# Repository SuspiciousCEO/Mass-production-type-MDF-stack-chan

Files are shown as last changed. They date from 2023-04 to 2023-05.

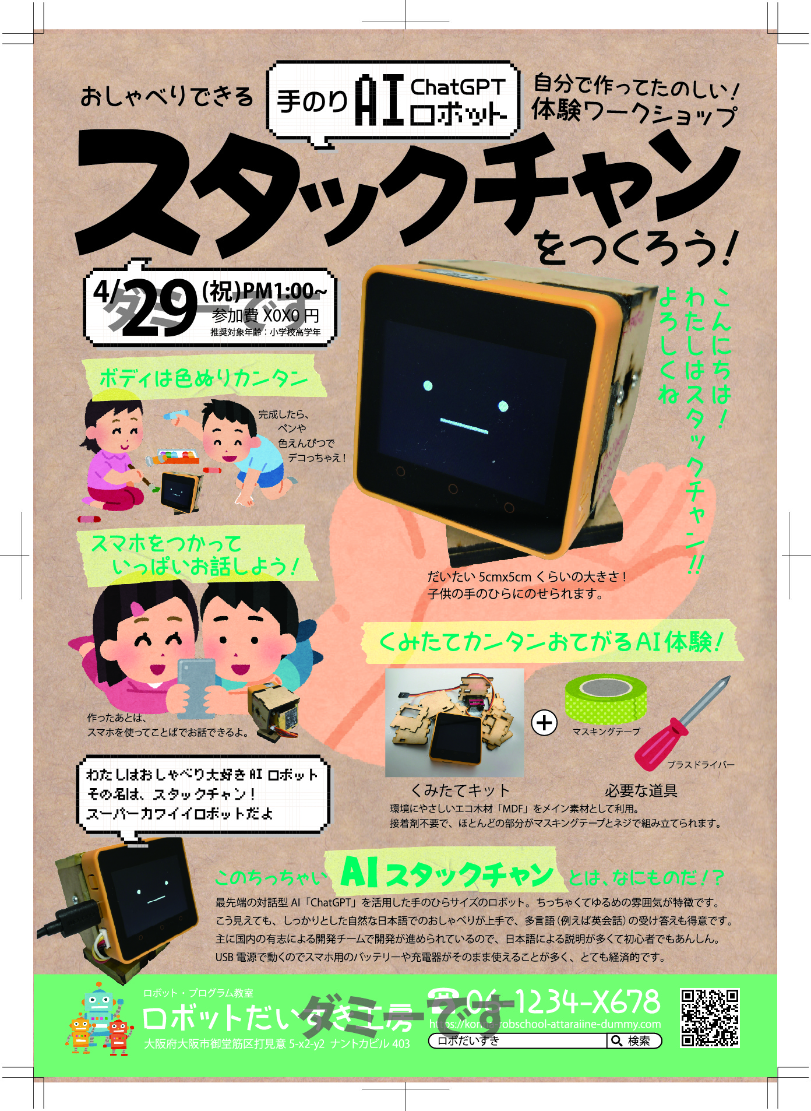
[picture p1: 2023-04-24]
FlyerDummy230327A.jpg

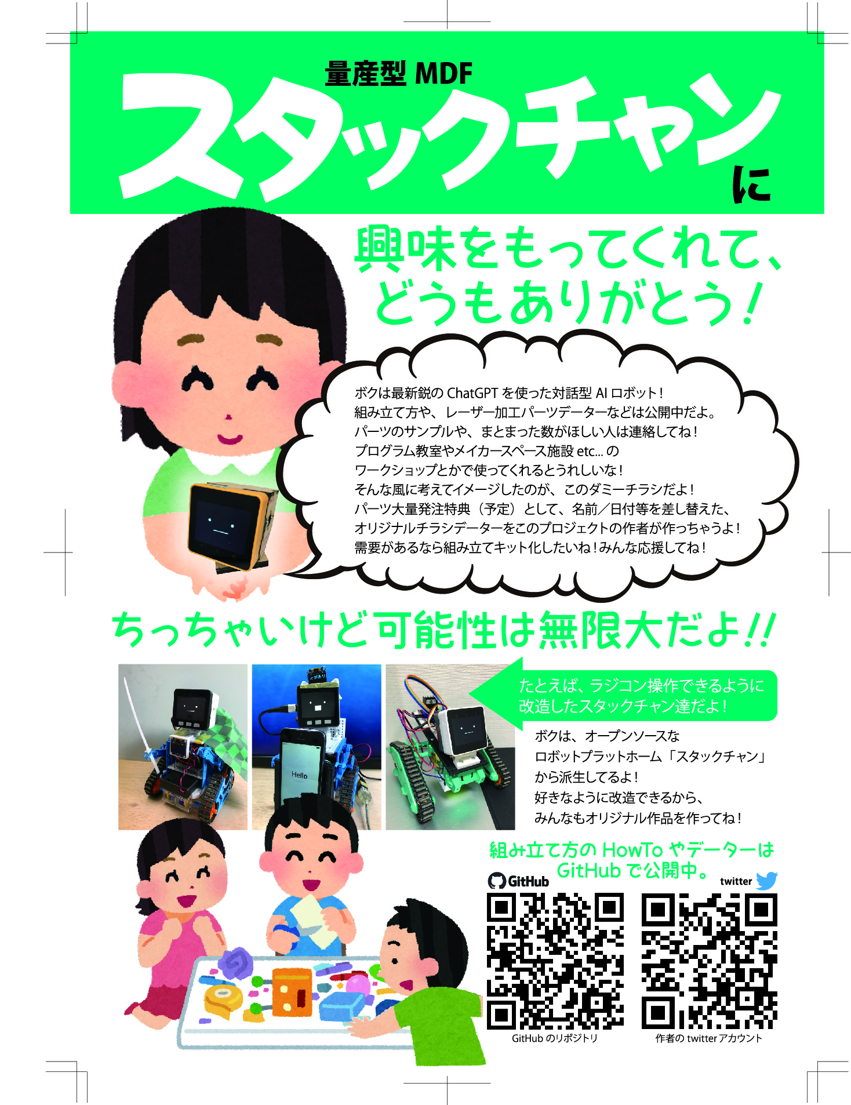
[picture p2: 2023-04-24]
FlyerDummy230327B.jpg

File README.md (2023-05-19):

# 量産型MDFｽﾀｯｸﾁｬﾝ



これはスーパーカワイイロボット [ｽﾀｯｸﾁｬﾝ(Stack-chan)](https://github.com/meganetaaan/stack-chan)
を量産しやすいように筐体ボディケースをMDF2.5mm厚用に設計したものです。
可能なかぎり、オリジナルのｽﾀｯｸﾁｬﾝSG90版筐体ボディとの動作の互換性を持たせています。
筐体ボディは共通部分が多いので、他の派生ｽﾀｯｸﾁｬﾝ（たとえば[AIｽﾀｯｸﾁｬﾝ](https://github.com/robo8080/M5Unified_StackChan_ChatGPT)
など）でもそのまま使うことが可能でしょう。

※写真は開発途中のものです。

## 特徴

オリジナルの[3Dプリンター版ｽﾀｯｸﾁｬﾝ](https://github.com/meganetaaan/stack-chan/tree/dev/v1.0/case)に比べ以下の点が優れています。





### 組み立てと分解が簡単
**小学生高学年でも作れそうなレベルを目指しました。**
たとえ破損したとしてもそのパーツの部分だけを追加で用意することで、全体のパーツを無駄にすることなく組み立てを再開することが可能です。
後述しますが、材料が安価なので失敗に対しての心構えが楽ですし、予備を多めに用意したとしても予算を圧迫しません。

### 適度な難易度とスピード感
材料が揃っていれば慣れてくると大人なら30分ぐらいで物理的な組み立て完了が可能。
失敗や手戻りがあったとしても、マスキングテープを剥がせばいいだけなので、特にパーツが痛むこともなく再開できます。
接着剤だと、固まり切ったらやり直しが難しいでしょうからこうはいきません。
あらかじめ時間枠が決まっている授業やワークショップなどでの活用に適しています。

### 圧倒的な生産性
レーザー加工機でパーツを切り出して用意するのに、一体につき10分もかかりません。(20Wくらいの出力ができる機種を想定)
3Dプリンター版を出力した場合、一体につき約半日〜1日の時間が必要となります。
また3Dプリンターによる造形物出力は、時には失敗することもあります。
期日までにまとまった数を用意することが必要な教育現場において、生徒全員に行き渡らせる必要がある教材を3Dプリンター出力に頼るのは不安が残りますが、
この量産型であればそういった懸念を払拭できます。

### 安い！コストパフォーマンス良好
筐体ボディ部分がMDF2.5mm厚板A5サイズで1枚に収まるので、極めて安価。
これ以外に組み立てで必要となる部品。すなわち頭脳部分になるマイコンM5Stackとサーボモーター類に予算を振り分けることが可能です。

### 安全性について
パーツさえそろっていれば、ボンドや接着剤類を使わなくても組み立てが可能。（もちろん使ってもOK）
組み立てに必要な道具はマスキングテープとプラスドライバー、あとお好みで結束バンドを。
刃物を使ったりしないのでケガをしにくいです。

### カスタマイズできる
子供達でも扱いが容易な3DCADソフトウェアのTinkercadで[プロジェクトデーター](https://www.tinkercad.com/things/7WoQx0e2Eym)を公開しているので、
その気になれば自由に再設計が可能です。

### 木のぬくもり感と後加工が容易
MDFは木材と紙の両方の雰囲気があるので、絵具などで色塗したり。ハサミなどであとからチョキチョキも可能。
キリやピンバイス（ハンドドリル）で穴あけも容易です。
紙を貼り合わせる場合でも水性のりでくっつくので接着剤を必要としません。
組み立て後も、カスタマイズの自由度が高いので自分ならではのオリジナル作品にすることができます。

### 持ち運びしやすい
組み立てやすくて、分解しやすいので、マスキングテープを剥がせば再び平面状にすることが可能。
よって普通郵便やメール便などで低コストに発送が可能です。
オリジナル版は約5cm立方サイズよりも小さくすることができないので、発送方法は少し考える必要があります。

## 欠点（ただし解決策や妥協点はあり）


### レーザー加工機が必要
あらかじめ、レーザー加工機でMDF板からパーツを切り出す必要があります。
（もちろんカッターナイフを使って手で切り出すことも可能かもしれませんがおすすめしません。）
レーザー加工機は個人宅で所有運用するには敷居が高いものですが、
教育機関やFab施設やホームセンターなどでも加工を請け負う場所が増えています。
それら加工業者などに依頼すれば比較的安価に切り出し加工が可能です。

### ススや焦げがある
レーザー加工機で焼き切っているので、どうしてもコゲとススはご愛嬌です。
気になるようでしたら、作業前に使い古しの歯ブラシでこすったり、ウェットティッシュで拭き取ってみてください。
ダイレクトに水洗いするとMDFは木と紙の間くらいの材質なので、ふやけてモロモロになってしましますので注意。

### 精度がすこしゆるい。
ハンドメイドなのでどうしても精度が甘くなりがちですが、ある程度ユルくても問題なく動くのであまり気にしなくてもいいです。

### 全てのサーボモーターに適合するかはやってみなければわからない
SG90というホビー向けサーボモーターは類似品が多く出回っており、入手性が良好な反面、おかげで動作やサイズに個体差やばらつきがあり、相性問題が発生します。必ずしも挙動やサイズ寸法がまったく同じというわけにはなっていません。

## 必要なもの


●本データーで切り出したMDF2.5mm厚パーツ一式、（2.5mm厚であればベニア等でも可）

●M5Stack CORE2（構成がほぼ同一のAWS版やおそらくBasicでも可）

●SG90系サーボモーター2個（サーボホーンやネジ類も付属してることが多いです。）

●[専用基板](https://github.com/akita11/Stack-chan_Takao_Base)

●Groveケーブル

●M3x6mmナベネジ1本

●M3x10mmナベネジ2本
※M3x10座金組込みねじ(セムスねじ)でもOK

●M3x18mmナベネジ4本
※Basicの場合、2本のみ、また18mmは長すぎるので付属スペーサーを追加するとよい

●M3ナット2個

●M3x6mmタップタイトねじPナベ4本

●SG90系サーボモーター2個

●マスキングテープ

●+ドライバー

●結束バンド （お好みで。）

●木工ボンド（マスキングテープの強度では不満がある場合はお好みで。）

## 組み立て方（マスキングテープ版）


### パーツAを2枚重ねて貼り合わせる


### パーツAを骨組みにして、パーツB・C・Dを組み合わせて貼る。これをヘルメット部分としておきます。



### 足部分を作る。パーツE・F・Eをはさんで貼る。



### パーツHに[専用基板](https://github.com/akita11/Stack-chan_Takao_Base)を取り付ける



輪っかの形をしているスペーサーを間にはさみながら、M3x10ネジとナットを使って締め付けます。

外側＞ [M3x6ネジ] | [パーツH] | [スペーサー] | [専用基板] | [ナット] ＜内側

### 胴体部分を作る。パーツG・H・I・J・Kを組み合わせて、箱状態にする。



### 足部分（パーツE・F・E）にサーボホーンをサーボモーターに付属のネジで固定。



サーボホーンの向きに注意。真ん中の形状をよく見て、細かいギザギザが中央部分にあるのがサーボモーター内側になります。
このとき使うサーボモーターに付属しているネジは、先が少し尖っているので注意。

### 胴体部分にサーボモーター2個を取り付ける。M3x6mmタップタイトねじPナベネジで固定。



先に下部の足用サーボモーターを取り付けてから、ヘルメット用のサーボモーターを取り付けます。
この時、ネジがすこし斜めになりやすいので、なるべく垂直にネジを締めましょう。

### ケーブルをまとめます。



ケーブル類が長くて邪魔なので、なるべく胴体内に束ねるように詰め込みます。
このとき、あとの作業がやりやすいように、胴体の穴からコネクター部分を外へくぐらせておきましょう。

### 結束バンドでケーブルを束ねてしばります。


結束バンドをしばって余った部分は、ニッパーなどで切りとりますが、切り口の先が尖らないように注意。

### ヘルメット部分にサーボホーンを取り付けます。



サーボホーンの片方が長くてジャマになるので、ニッパーなどですこし先の部分を切りとります。このとき使うサーボモーターに付属しているネジは、先が少し尖っているので注意。

### 胴体とヘルメット部分をつなげ合わせます。



サーボモーターの軸とサーボホーンの穴に合わせてはめ込みます。
ここはすこし難しいかもしれませんので、ヘルメット部分を手ですこし広げて強引に入れるか、一度ヘルメット部分のテープをはがして分解してからサーボホーンの穴に合わせてはめ込んだ後、再度ヘルメット部分を貼り合わせて元に戻すようにしてみるのも良いでしょう。

### サーボモーターとサーボホーンをねじ止めします。



先にM3x6mmタップタイトねじPナベをサーボに仮でネジ締めを通したほうがあとあとやりやすい。
足部分の裏側からサーボモーターをねじ止めします。同様にヘルメット部分のサーボモーターもねじ止めします。

### ヘルメット部分にM5Stack本体を裏側からネジ止めします。



M3x18mmナベねじを使って固定します。あまりキツくしめると、液晶画面を痛めるのでほどほどに。ネジ穴部分に指が届きにくいのですこしコツがいります。難しいようでしたら、一度ヘルメット部分のテープをはがして分解してからネジ止めして、再度ヘルメット部分を貼り合わせて元に戻すようにしてみるのも良いでしょう。

### 仕上げにGroveコネクタをM5Stack本体側面につなげて完成。



ヘルメット部分の残ったネジ穴にM3x6mmナベねじを少しゆるめに入れます。ネジは空回りするのですが、それが正解です。軸の固定は反対側のサーボホーンでしっかり強度があるのであまり気にしないで。最後にGroveコネクタをM5Stack本体側面につなげて完成です。

## その他



量産型ロボットの様式美として、稼働範囲の自由度を上げるために、動力線を一部筐体ボディ外部に露出させてあります。

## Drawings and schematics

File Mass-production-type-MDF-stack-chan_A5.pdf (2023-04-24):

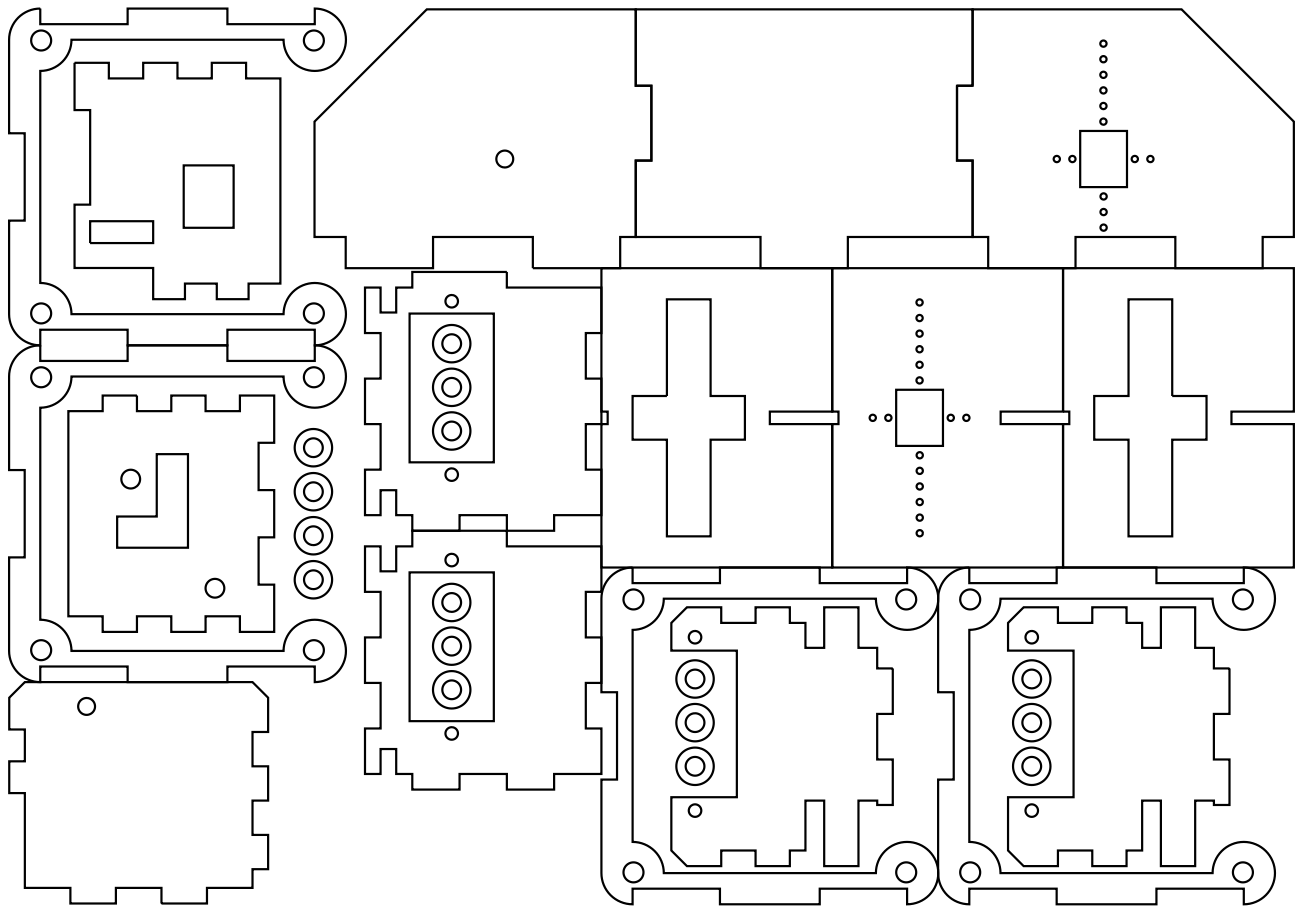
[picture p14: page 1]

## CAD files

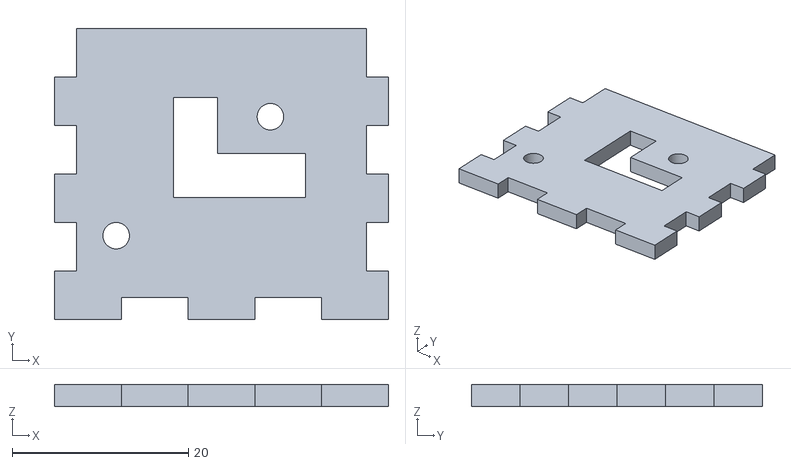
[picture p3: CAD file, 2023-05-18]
MDFstackchanH.stl
37.9 x 33.0 x 2.50

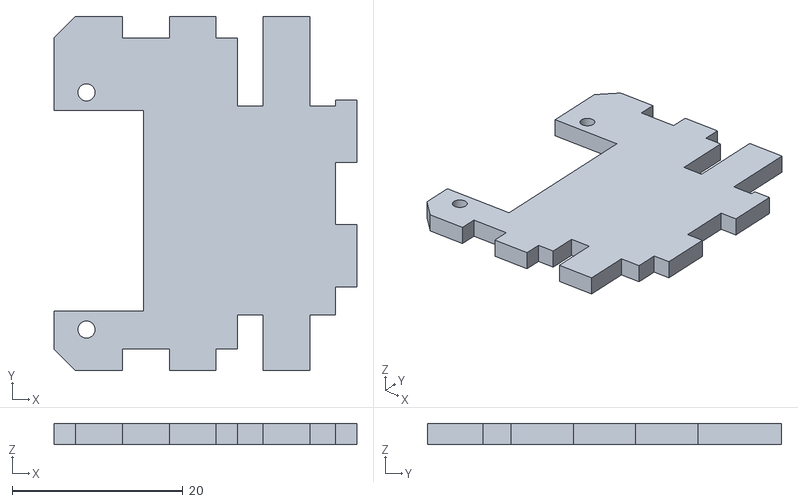
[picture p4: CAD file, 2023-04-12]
MDFstackchanJ.stl
35.5 x 41.5 x 2.50

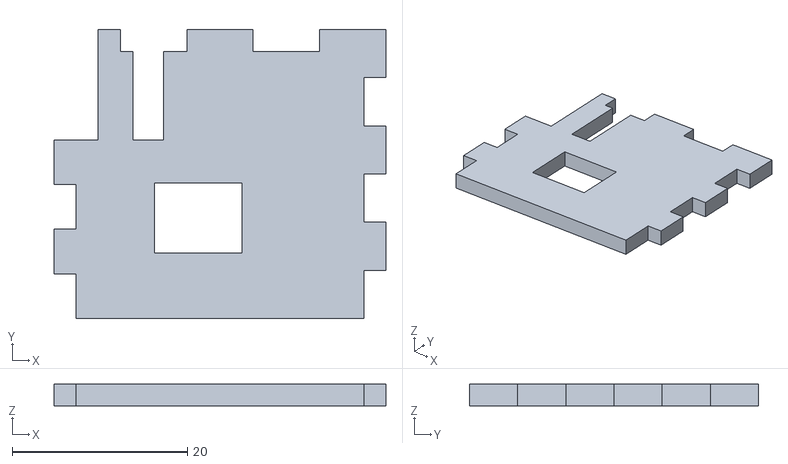
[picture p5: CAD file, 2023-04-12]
MDFstackchanG.stl
37.9 x 33.0 x 2.50

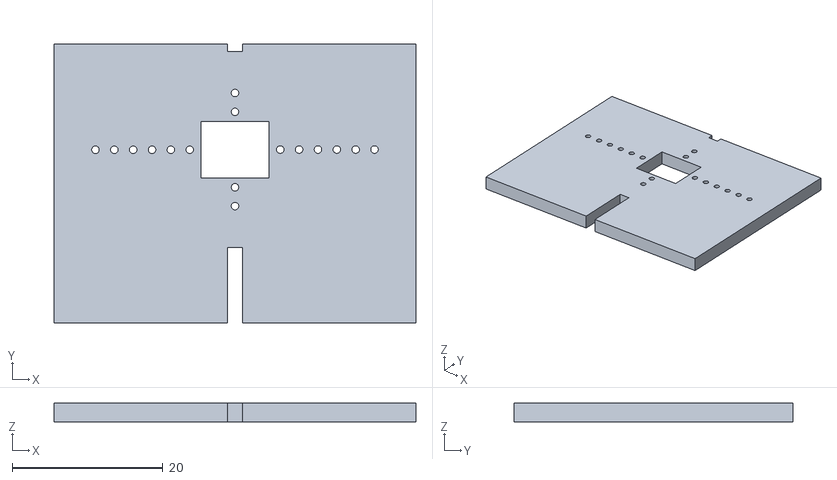
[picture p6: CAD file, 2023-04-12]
MDFstackchanF.stl
48.0 x 37.0 x 2.50

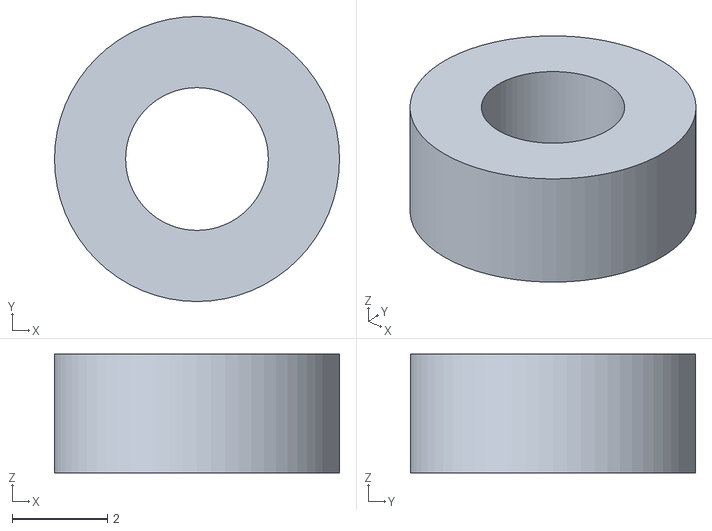
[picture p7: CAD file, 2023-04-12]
MDFstackchanL.stl
6.00 x 6.00 x 2.50

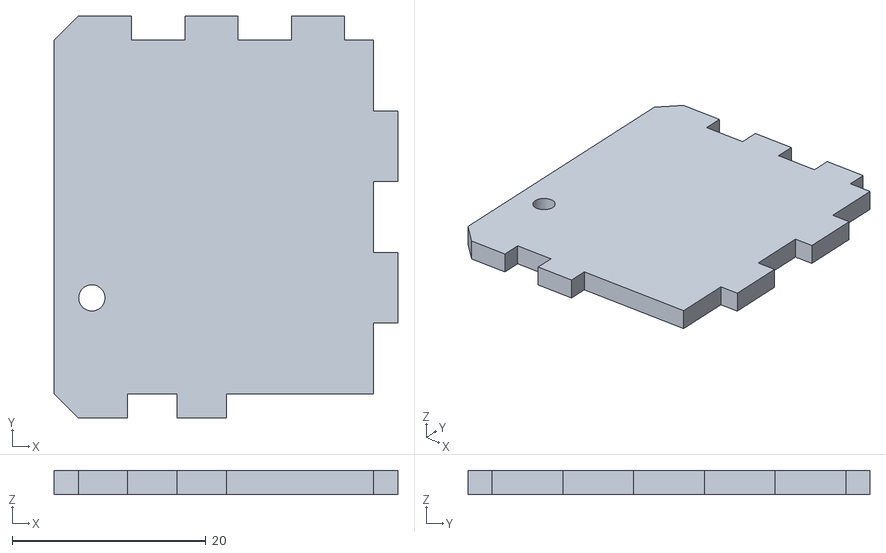
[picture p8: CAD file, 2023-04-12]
MDFstackchanI.stl
35.5 x 41.5 x 2.50

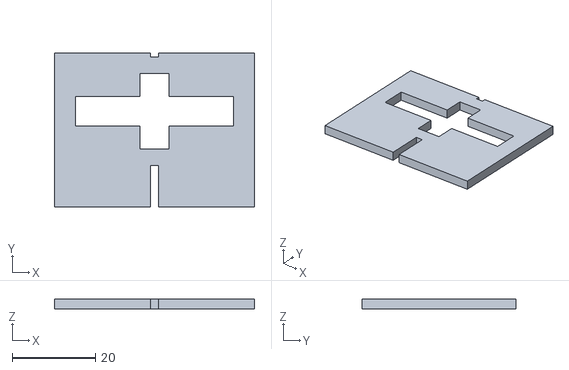
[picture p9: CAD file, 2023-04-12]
MDFstackchanE.stl
48.0 x 37.0 x 2.50

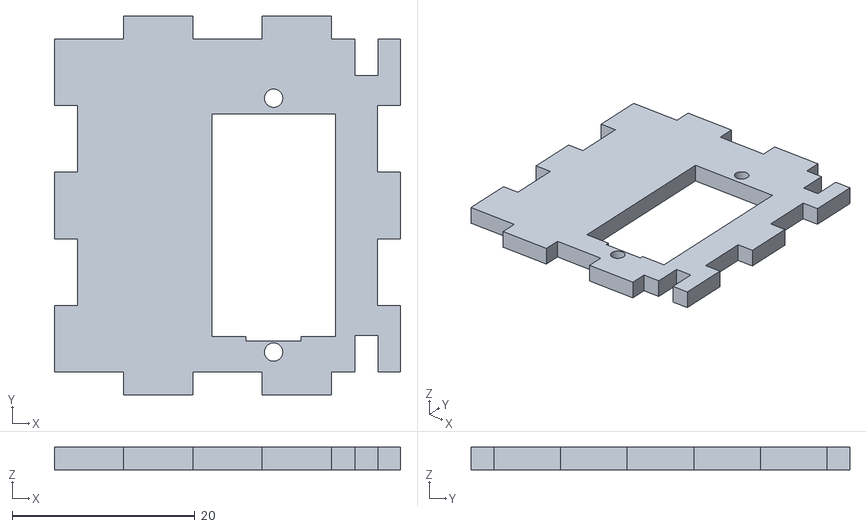
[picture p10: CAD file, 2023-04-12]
MDFstackchanK.stl
37.9 x 41.5 x 2.50

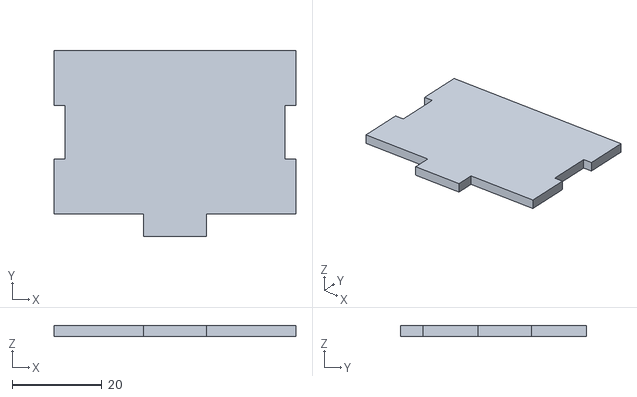
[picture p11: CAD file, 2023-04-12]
MDFstackchanB.stl
54.0 x 41.5 x 2.50

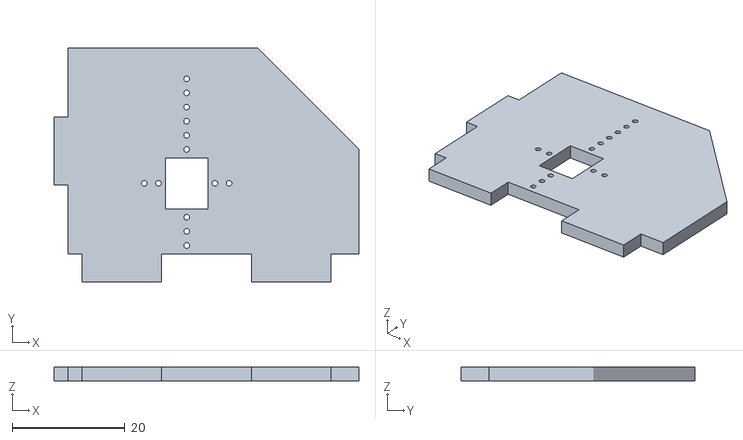
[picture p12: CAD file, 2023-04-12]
MDFstackchanD.stl
54.0 x 41.5 x 2.50

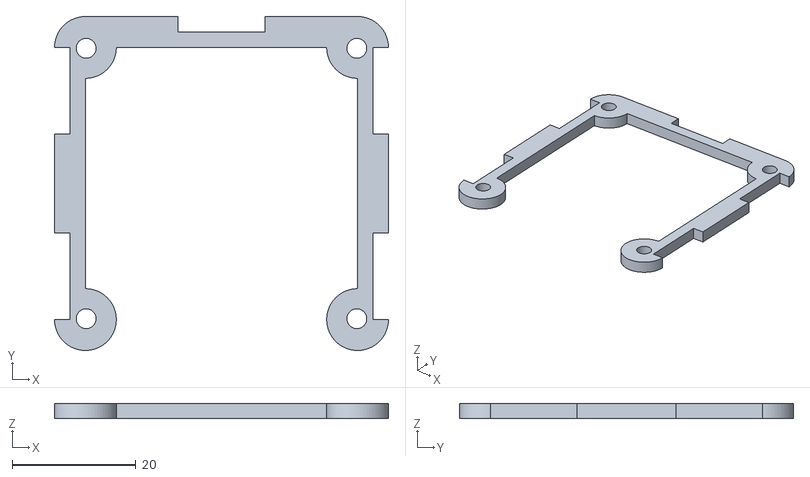
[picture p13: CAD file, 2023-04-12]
MDFstackchanA.stl
54.0 x 54.0 x 2.50

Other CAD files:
MDFstackchanC.stl
